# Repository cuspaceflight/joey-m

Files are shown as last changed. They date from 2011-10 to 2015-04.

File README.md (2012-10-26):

JOEY-M - CU Spaceflight
====================

Joey-M is an experimental flight computer produced as part of the Wombat flight
computer project at Cambridge University Spaceflight.  

It uses a twin varactor crystal pulling arrangement to change the transmit
frequency of a Micrel MICRF112YMM 434MHz ISM band transmitter, along with a dual
DAC from Linear Technology to control the varactor bias voltages.  

The DAC can be any of the LTC range in MSOP-8 package which share a footprint, 
including the LTC1661/1662 (10 bit), LTC2622 (12 bit), LTC2612 (14 bit)
and LTC2602 (16 bit).  

Other equipment on board is a uBlox NEO-6Q GPS, TMP100 12 bit temperature
sensor, and an Atmel ATMEGA328P MCU.  

Designed and released into the public domain by Jon Sowman - March 2012.  

[Contact CUSF](mailto:contact@cusf.co.uk)

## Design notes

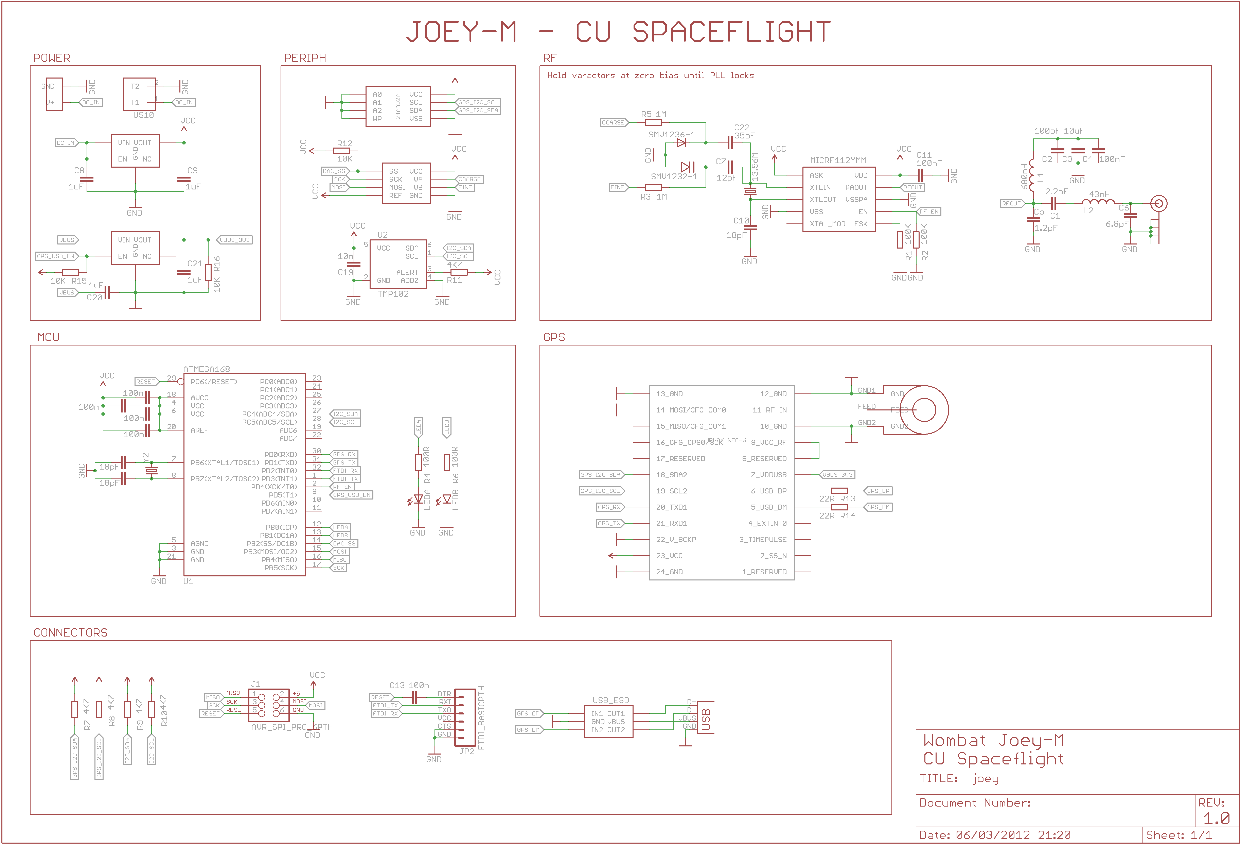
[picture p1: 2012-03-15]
pcb/joey-m.png

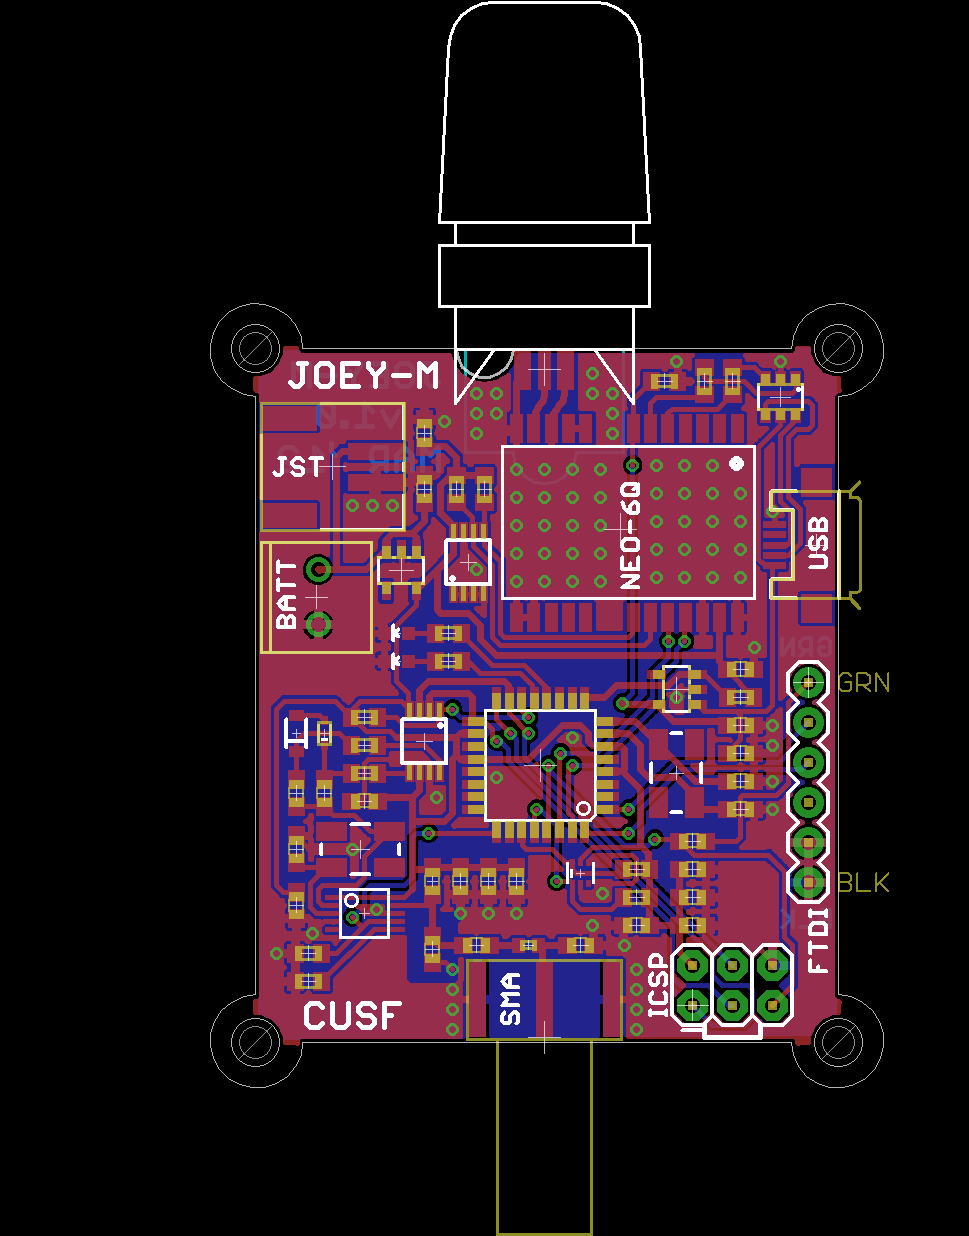
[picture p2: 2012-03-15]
pcb/joey-m-brd.png

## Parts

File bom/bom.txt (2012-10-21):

  PART         QTY             DESCRIPTION               TYPE            LIST
  ==========================================================================
1715486         1       ATMEL AVR ATMEGA328             TQFP32          £4.25
1494165 	1 	MICREL MICRF112YMM UHF    	MSOP10    	£3.28
1753780         1 	RF VARACTOR DIODE SMV1232  	SC79     	£0.74
1753783         1 	RF VARACTOR DIODE SMV1236  	SOD-323     	£0.54
1858064         2       IC, LDO, 3.3V, 0.3A, 5TSOT      5-TSOT          £0.89
1269406         1       ESD PROTECTION, SMD             SOT-23-6        £0.56
1331296         1       24AA32A I2C EEPROM              MSOP8           £0.40
1342651         1       JACK SMA, END LAUNCH            BULKHEAD        £2.93
1234659         1       TMP100 IC, SOT-23-6             SOT23-6         £2.22
1330944         1       DAC, DUAL 16-BIT                MSOP8           £8.88
1098611         1       TERMINAL BLOCK, 2WAY            PTH             £0.21
9492615         1       JST, SIDE ENT, 2WAY             SMD             £0.34
1521869         1       MICRO USB AB RECEPT             SMD             £0.67
1248132         1       ICSP HEADER 2x3 PTH 0.1"        PTH             £0.24
1841236         1       HEADER, 2.54MM, PIN, 32WAY      PTH             £1.88
1841971 	1 	13.56MHz XTAL 5x3mm      	SMD       	£0.59
1640930         1       16.00MHz XTAL 5.3mm             SMD             £1.62
1650686         1       BATT HOLDER AAA, LEADED         N/A             £1.20
-- PASSIVES
1469748         3       RESISTOR 10KR 0.1W              0603            £0.01
1738931         2 	RESISTOR 0.1W 100KR       	0603      	£0.02
9330364         2       RESISTOR 100R                   0603            £
2008367         2       RESISTOR 1MR                    0603            £0.01
2008358         4       RESISTOR 4K7                    0603            £0.01
2008345         2       RESISTOR 22R                    0603            £0.01
1833863         8 	CAPACITOR 100nF           	0603      	£0.01
1833804         1       CAPACITOR, 6.3V, 10UF           0603            £0.15
1833809         4       CAPACITOR 1UF                   0603            £0.02
1327675         1       CAPACITOR 10NF                  0603            £0.02
1748739         1 	INDUCTOR 43nH             	0402      	£0.28
1343111 	1 	INDUCTOR 680nH            	0603      	£0.16
1328308         1       LED RED                         0603            £
1328306         1       LED GREEN                       0603            £
-- C0G CAPS
1865478         1       CAPACITOR 36PF                  0603            £0.01
1828907         1       CAPACITOR 12PF                  0603            £0.01
1414620         3       CAPACITOR 18PF                  0603            £0.03
1865503         1       CAPACITOR 6.8PF                 0603            £0.04
1457729         1       CAPACITOR 1.2PF                 0603            £0.13
1813415         1       CAPACITOR 2.2PF                 0603            £0.03
9406115         1       CAPACITOR 100PF                 0603            £0.02
-- OTHER
SARANTEL SL1202 ANTENNA
UBLOX NEO-6Q GPS

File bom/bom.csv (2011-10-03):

Line Number | Order Code | Qty | Product Description | Manufacturer Name & Part No. | RoHS | List Price | Availability | Line Price | Line note
1 | 1753785 | 2 | RF TUNING VARACTOR DIODE | SKYWORKS SOLUTIONS INC - SMV1249-079LF | YES | 0.4536 | In Stock | 0.91 | RF TUNING VARACTOR DIODE
2 | 1189327 | 1 | CAPACITOR, VARIABLE, 5 TO 20PF | AVX - CTZ2E-20C-W2-P | YES | 0.6237 | In Stock | 0.62 | VARIABLE CAPACITOR 5-20pF
3 | 1865473 | 10 | CAPACITOR, NP0, 0603, 50V, 13PF | KEMET - C0603C130J5GACTU | YES | 0.0105 | In Stock | 0.11 | CAPACITOR 13pF 50V
4 | 1841971 | 1 | XTAL, 13.560MHZ, 18PF, SMD, 5.0X3.2 | TXC - 7B-13.560MAAJ-T | YES | 0.5913 | In Stock | 0.59 | 13.560MHz XTAL 5x3mm
5 | 1494165 | 1 | TRANSMITTER, ASK/FSK, UHF, MSOP10 | MICREL SEMICONDUCTOR - MICRF112YMM | YES | 2.66 | In Stock | 2.66 | MICREL MICRF112YMM UHF
6 | 721852 | 10 | CAPACITOR, 0603, 1.20PF, 50V | YAGEO (PHYCOMP) - CC0603CRNPO9BN1R2 | YES | 0.0275 | In Stock | 0.28 | CAPACITOR 1.2pF
7 | 1343111 | 5 | INDUCTOR, 0603 CASE, SHIELD, 680NH±10% | MURATA - LQM18NNR68K00D | YES | 0.1571 | In Stock | 0.79 | INDUCTOR 680nH
8 | 1650758 | 1 | CAPACITOR, CERAMIC MULTILAYER | JOHANSON TECHNOLOGY - 251R14S2R2BV4T... | YES | 0.0486 | In Stock | 0.05 | CAPACITOR 2.2pF
9 | 8819807 | 10 | CAPACITOR, 0603, 6.8PF, 50V | MURATA - GRM1885C1H6R8DZ01D | YES | 0.0397 | In Stock | 0.4 | CAPACITOR 6.8pF
10 | 9406115 | 10 | CAPACITOR, 0603, 100PF, 50V | MULTICOMP - U0603C101JCT | YES | 0.0154 | In Stock | 0.15 | CAPACITOR 100pF
11 | 1833863 | 10 | CAPACITOR, 0603, X7R, 16V, 100NF | AVX - 0603YC104K4T4A | YES | 0.0122 | In Stock | 0.12 | CAPACITOR 100nF
12 | 1627775 | 10 | RESISTOR, SURGE, 10K, 1%, 0603 | KOA - SG73S1JTTD1002F | Y-EX | 0.0251 | In Stock | 0.25 | RESISTOR 63mW 10KR
13 | 1294515 | 5 | CAPACITOR, 0603, 9.1PF, 200V, C0G | MURATA - ERB1885C2D9R1CDX5D | YES | 0.0494 | In Stock | 0.25 | CAPACITOR 9.1pF
14 | 1738931 | 25 | RESISTOR, 0603, 1%, 100K | VISHAY DRALORIC - CRCW0603100KFKEAHP | Y-EX | 0.0243 | In Stock | 0.61 | RESISTOR 0.1W 100KR
15 | 1668492 | 1 | HEADER, 2.54MM, SINGLE, 4WAY | SAMTEC - TLW-104-05-G-S | YES | 0.4698 | In Stock | 0.47 | 4x1 HEADER PC BOARD
16 | 1748739 | 3 | INDUCTOR, 0402, 43NH, 100MA | WUERTH ELEKTRONIK - 744765143A | YES | 0.2754 | In Stock | 0.83 | INDUCTOR 43nH
17 | 1463375 | 2 | CAPACITOR, 0603, 10UF, 6.3V, X5R | TAIYO YUDEN - JMK107BJ106MA-T | YES | 0.4455 | In Stock | 0.89 | CAPACITOR 10uF
 |  |  |  |  |  |  | Goods Subtotal: | 9.98
 |  |  |  |  |  |  | Promotion Code Discount: | 0.0
 |  |  |  |  |  |  | Delivery Charges | Unknown
 |  |  |  |  |  |  | Your Total Price: | 9.98
 |  |  |  |  |  |  | VAT | 2.0
 |  |  |  |  |  |  | Total (Excl Delivery) | 11.98

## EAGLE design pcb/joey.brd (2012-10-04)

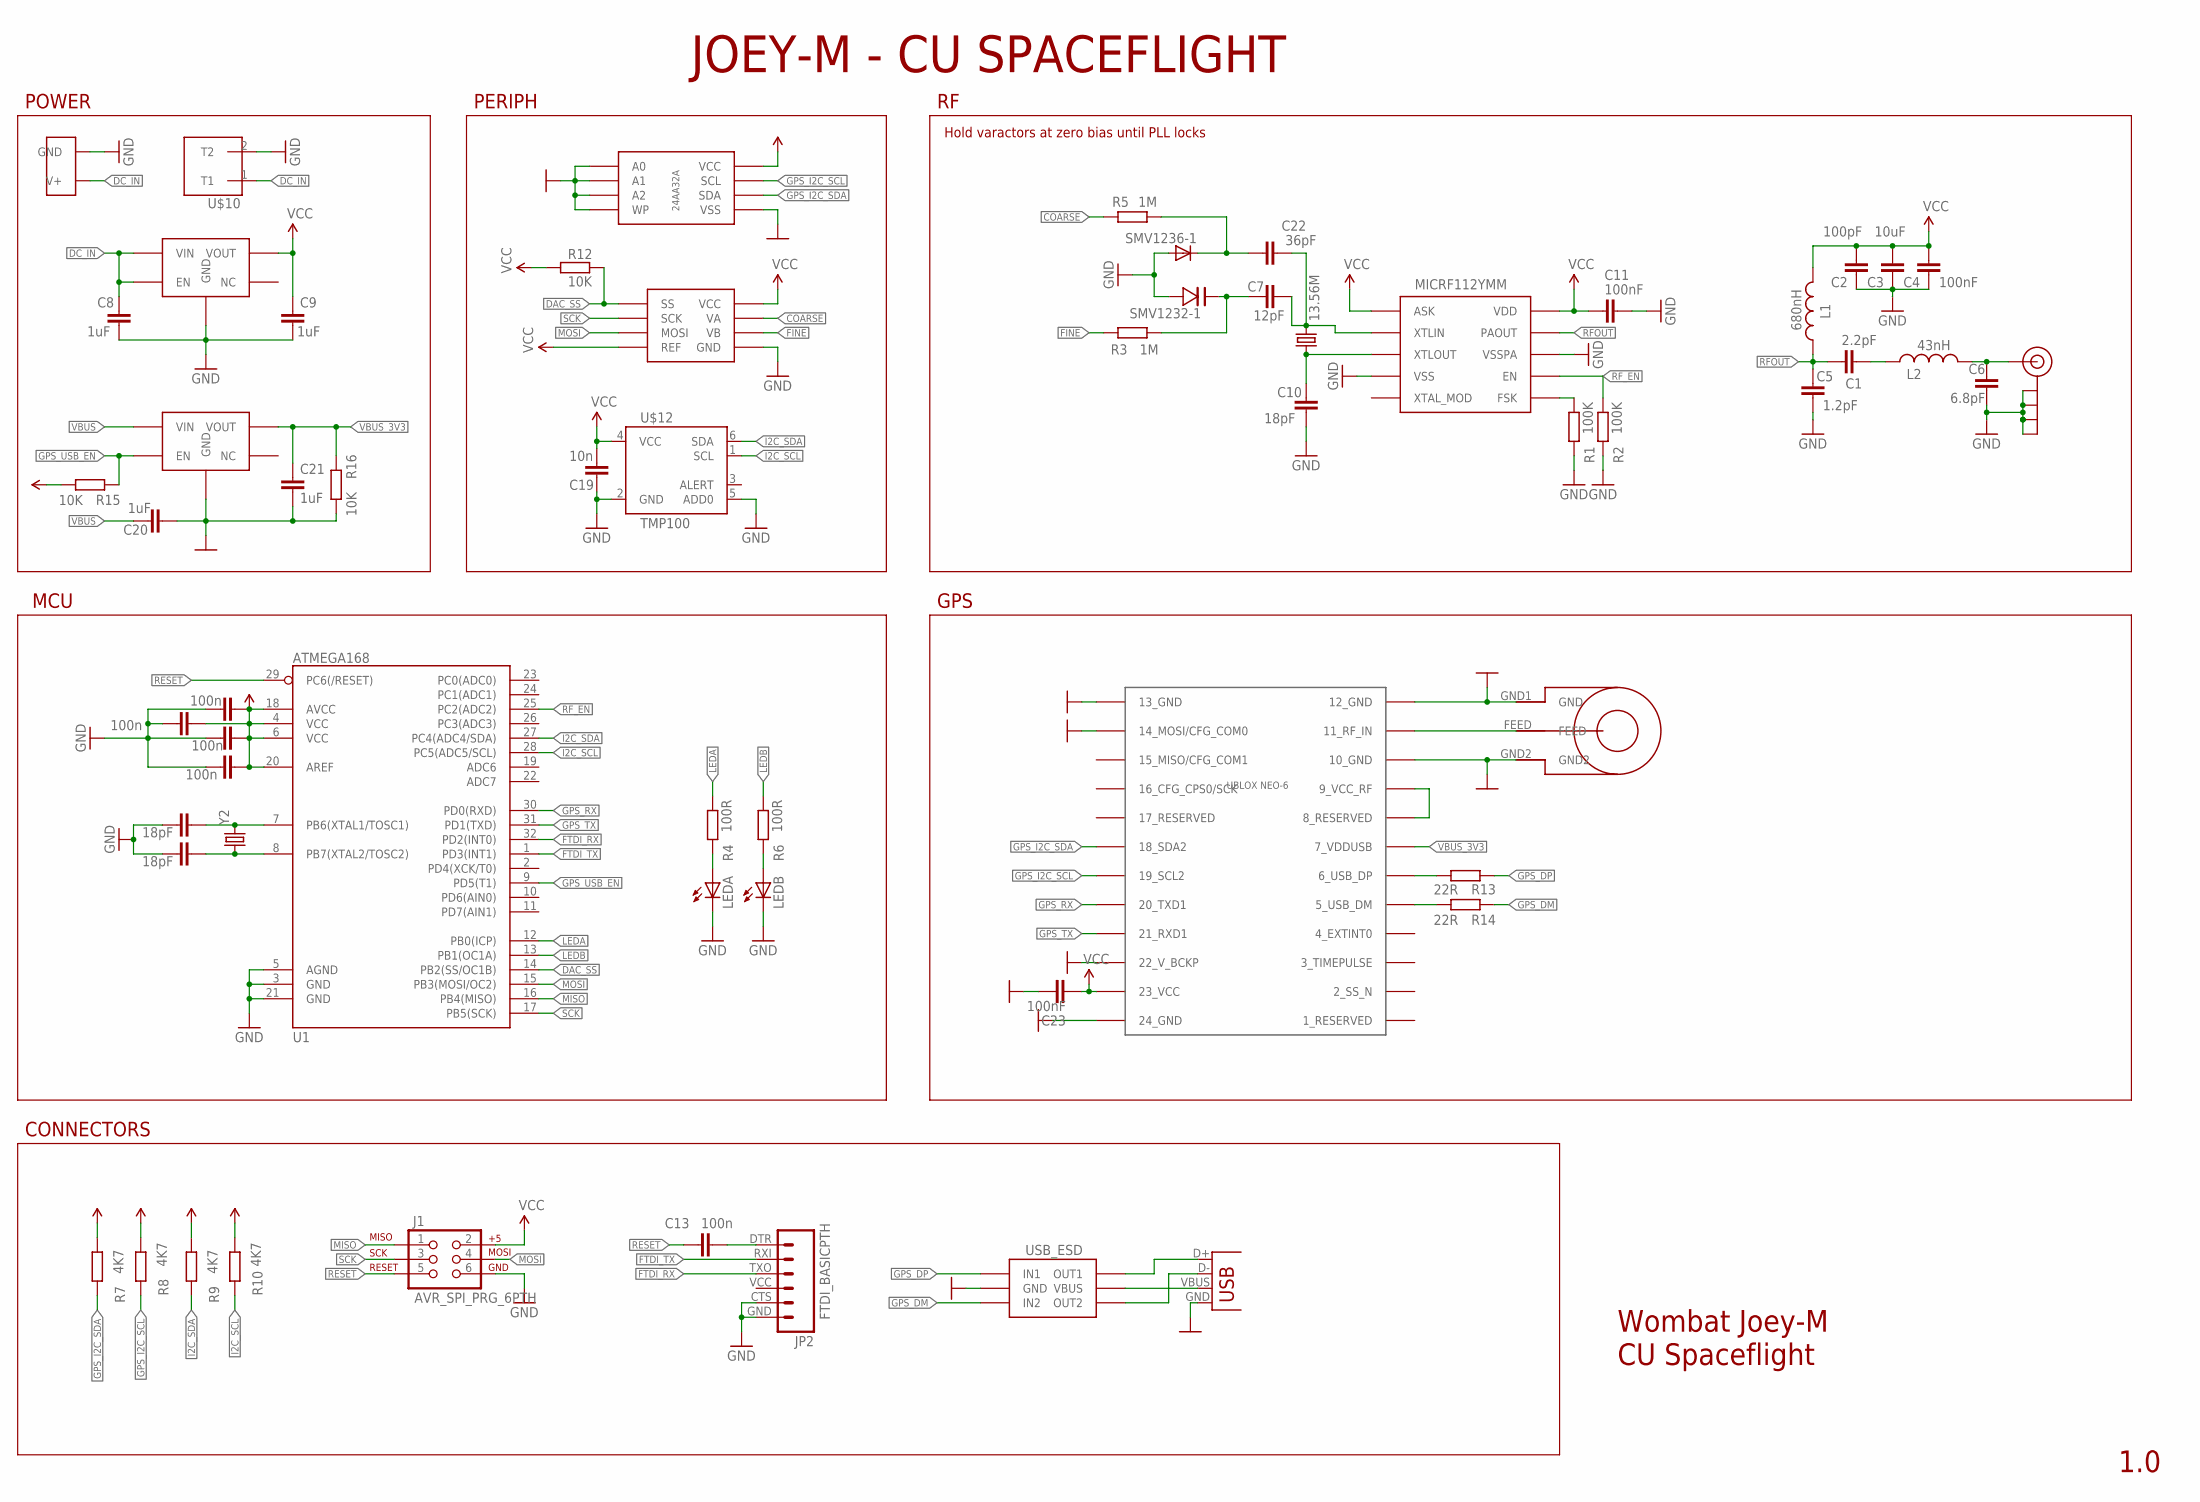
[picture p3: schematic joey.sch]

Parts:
C1: 2.2pF; C0603
C2: 100pF; C0603
C3: 10uF; C0603
C4, C11, C23: 100nF; C0603
C5: 1.2pF; C0603
C6: 6.8pF; C0603
C7: 12pF; C0603
C8, C9, C20, C21: 1uF; C0603
C10, C17, C18: 18pF; C0603
C12, C13, C14, C15, C16: 100n; C0603
C19: 10n; C0603
C22: 36pF; C0603
J1: AVR_SPI_PRG_6PTH; 2X3
JP2: FTDI_BASICPTH; FTDI_BASIC
L1: 680nH; 0603
L2: 43nH; C0402
LEDA: LED0603; LED-0603
LEDB: LED0603; LED-0603
R1, R2: 100K; R0603
R3, R5: 1M; R0603
R4, R6: 100R; R0603
R7, R8, R9, R10: 4K7; R0603
R12, R15, R16: 10K; R0603
R13, R14: 22R; R0603
SMV1232-1: SMV1247-VARACTOR; SMV1247-VARACTOR-SC-79
SMV1236-1: DIODESOD; SOD-323
U1: ATMEGA168; TQFP32-08
U$1: MICRF112; MICRF112-MSOP10
U$2: SARANTEL-SR1202
U$3: UBLOX_NEO-6; UBLOX_NEO-6P
U$4, U$9: ADP122AUJZ-3V3REG-5TSOT; SOT23-5L
U$5: JST_SMTSIDE; JST_CONN_SMD
U$6: I2C_EEPROM_24AA32A; MSOP8
U$7: SMA_END_19-70-TGG
U$8: LTC2602_16BIT_DUALDAC; MSOP8
U$10: TE_CONN_TERMBLK; 10A_TECONN_TERMBLK
U$12: TMP100; SOT23-6
USB_ESD: USB_ESD_PROT_USBLC6; SOT23-6
X1: USB-MICROB
Y1: 13.56M; CRYSTAL-SMD-5X3
Y2: CRYSTAL5X3; CRYSTAL-SMD-5X3

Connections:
COARSE: R5.1, U$8.8 (VA)
COARSE_V: C22.1, R5.2, SMV1236-1.1 (C)
DAC_SS: R12.2, U1.14 (PB2(SS/OC1B)), U$8.1 (SS)
DC_IN: C8.2, U$4.1 (VIN), U$4.3 (EN), U$5.VBATT (V+), U$10.1 (T1)
FINE: R3.2, U$8.5 (VB)
FTDI_RX: JP2.TXO (3), U1.32 (PD2(INT0))
FTDI_TX: JP2.RXI (2), U1.1 (PD3(INT1))
GND: C2.1, C3.1, C4.1, C5.1, C6.1, C8.1, C9.1, C10.1, C11.1, C12.2, C14.1, C15.1, C16.1, C17.2, C18.2, C19.1, C20.1, C21.1, C23.1, J1.6, JP2.CTS (5), JP2.GND (6), LEDA.C, LEDB.C, R1.1, R2.1, R16.2, SMV1232-1.AN (ANODE), SMV1236-1.2 (A), U1.3 (GND), U1.5 (AGND), U1.21 (GND), U$1.VSS, U$1.VSSPA, U$2.GND1 (GND), U$2.GND2, U$3.10_GND, U$3.12_GND, U$3.13_GND, U$3.14_MOSI/CFG_COM0, U$3.22_V_BCKP, U$3.24_GND, U$4.2 (GND), U$5.GND, U$6.1 (A0), U$6.2 (A1), U$6.3 (A2), U$6.4 (VSS), U$6.7 (WP), U$7.GND1 (GND), U$7.GND2 (GND), U$7.GND3 (GND), U$7.GND4 (GND), U$8.7 (GND), U$9.2 (GND), U$10.2 (T2), U$12.2 (GND), U$12.5 (ADD0), USB_ESD.2 (GND), X1.GND
GPS_DM: R14.1, USB_ESD.3 (IN2)
GPS_DP: R13.1, USB_ESD.1 (IN1)
GPS_I2C_SCL: R8.1, U$3.19_SCL2, U$6.6 (SCL)
GPS_I2C_SDA: R7.1, U$3.18_SDA2, U$6.5 (SDA)
GPS_RX: U1.30 (PD0(RXD)), U$3.20_TXD1
GPS_TX: U1.31 (PD1(TXD)), U$3.21_RXD1
GPS_USB_EN: R15.1, U1.9 (PD5(T1)), U$9.3 (EN)
I2C_SCL: R10.1, U1.28 (PC5(ADC5/SCL)), U$12.1 (SCL)
I2C_SDA: R9.1, U1.27 (PC4(ADC4/SDA)), U$12.6 (SDA)
LEDA: R4.2, U1.12 (PB0(ICP))
LEDB: R6.2, U1.13 (PB1(OC1A))
MISO: J1.1, U1.16 (PB4(MISO))
MOSI: J1.4, U1.15 (PB3(MOSI/OC2)), U$8.3 (MOSI)
unnamed: R1.2, U$1.FSK
unnamed: C10.2, U$1.XTLOUT, Y1.1
unnamed: C13.2, JP2.DTR (1)
unnamed: C7.2, C22.2, U$1.XTLIN, Y1.3 (2)
unnamed: C1.2, L2.1
unnamed: C6.2, L2.2, U$7.RF (SIGNAL)
unnamed: C7.1, R3.1, SMV1232-1.CAT (CATHODE)
unnamed: LEDA.A, R4.1
unnamed: C17.1, U1.7 (PB6(XTAL1/TOSC1)), Y2.3 (2)
unnamed: C18.1, U1.8 (PB7(XTAL2/TOSC2)), Y2.1
unnamed: U$2.FEED, U$3.11_RF_IN
unnamed: LEDB.A, R6.1
unnamed: U$3.8_RESERVED, U$3.9_VCC_RF
unnamed: USB_ESD.4 (OUT2), X1.D-
unnamed: USB_ESD.6 (OUT1), X1.D+
unnamed: R13.2, U$3.6_USB_DP
unnamed: R14.2, U$3.5_USB_DM
RESET: C13.1, J1.5, U1.29 (PC6(/RESET))
RFOUT: C1.1, C5.2, L1.1, U$1.PAOUT
RF_EN: R2.2, U1.25 (PC2(ADC2)), U$1.EN
SCK: J1.3, U1.17 (PB5(SCK)), U$8.2 (SCK)
VBUS: C20.2, U$9.1 (VIN), USB_ESD.5 (VBUS), X1.VBUS
VBUS_3V3: C21.2, R16.1, U$3.7_VDDUSB, U$9.5 (VOUT)
VCC: C2.2, C3.2, C4.2, C9.2, C11.2, C12.1, C14.2, C15.2, C16.2, C19.2, C23.2, J1.2, L1.2, R7.2, R8.2, R9.2, R10.2, R12.1, R15.2, U1.4 (VCC), U1.6 (VCC), U1.18 (AVCC), U1.20 (AREF), U$1.ASK, U$1.VDD, U$3.23_VCC, U$4.5 (VOUT), U$6.8 (VCC), U$8.4 (REF), U$8.6 (VCC), U$12.4 (VCC)

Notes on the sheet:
Wombat Joey-M
CU Spaceflight
1.0
Hold varactors at zero bias until PLL locks
JOEY-M - CU SPACEFLIGHT
POWER
MCU
GPS
PERIPH
CONNECTORS

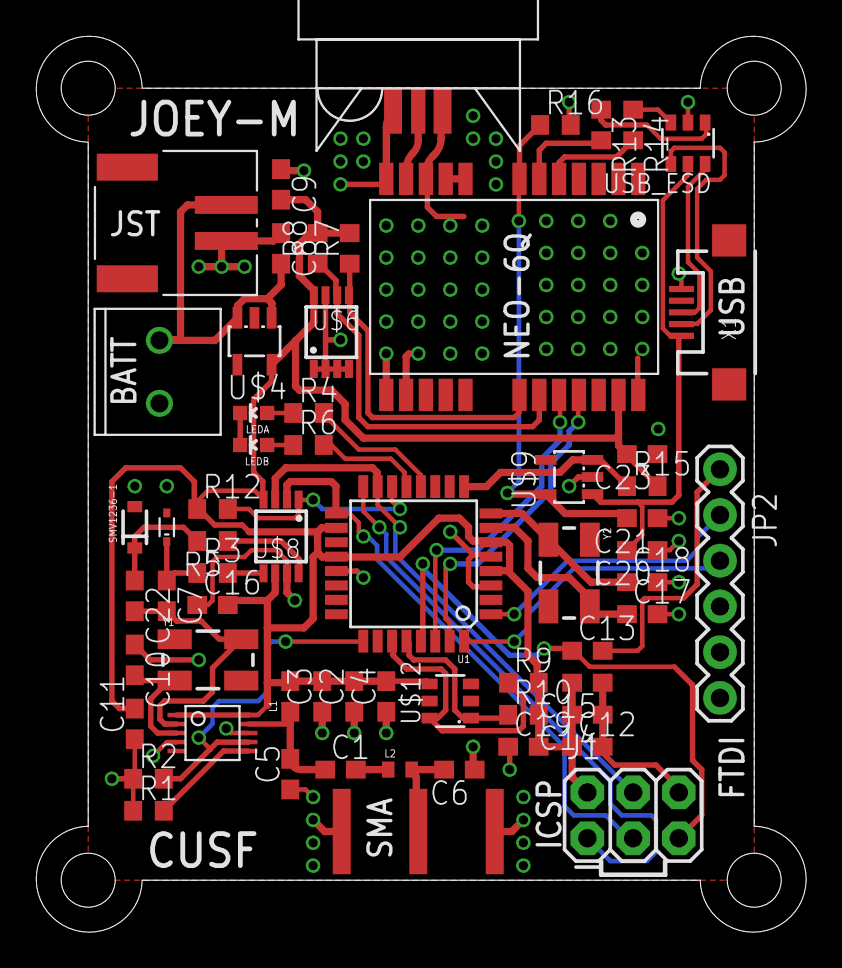
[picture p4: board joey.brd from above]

Board: 2 copper layers, 42.8 x 49.8 mm, 63 parts (1 on the bottom side), 45 nets.

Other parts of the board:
U$11: CUSF_LOGO_LARGE

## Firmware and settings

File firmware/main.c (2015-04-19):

/**
 * JOEY-M by CU Spaceflight
 *
 * This file is part of the JOEY-M project by Cambridge University Spaceflight.
 *
 * Jon Sowman 2012
 */

#include <avr/io.h>
#include <stdio.h>
#include <util/delay.h>
#include <avr/eeprom.h>
#include <avr/interrupt.h>
#include <string.h>
#include <stdbool.h>
#include <stdlib.h>
#include <avr/wdt.h>

#include "led.h"
#include "radio.h"
#include "gps.h"

// 30kHz range on COARSE, 3kHz on FINE

char s[100];
uint32_t EEMEM ticks = 0;

int main()
{
    // Disable, configure, and start the watchdog timer
    wdt_disable();
    wdt_reset();
    wdt_enable(WDTO_8S);

    // Start and configure all hardware peripherals
    sei();
    led_init();
    radio_init();
    gps_init();
    radio_enable();

    // Set the radio shift and baud rate
    _radio_dac_write(RADIO_COARSE, RADIO_CENTER_FREQ);
    _radio_dac_write(RADIO_FINE, 0);
    radio_set_shift(RADIO_SHIFT_425);
    radio_set_baud(RADIO_BAUD_50);

    // Radio chatter
    for(uint8_t i = 0; i < 5; i++)
    {
        radio_chatter();
        wdt_reset();
    }
    
    int32_t lat = 0, lon = 0, alt = 0;
    uint8_t hour = 0, minute = 0, second = 0, lock = 0, sats = 0;

    while(true)
    {
        led_set(LED_GREEN, 1);

        // Get the current system tick and increment
        uint32_t tick = eeprom_read_dword(&ticks) + 1;

        // Check that we're in airborne <1g mode
        if( gps_check_nav() != 0x06 ) led_set(LED_RED, 1);

        // Get information from the GPS
        gps_check_lock(&lock, &sats);
        if( lock == 0x02 || lock == 0x03 || lock == 0x04 )
        {
            gps_get_position(&lat, &lon, &alt);
            gps_get_time(&hour, &minute, &second);
        }

        led_set(LED_GREEN, 0);

        // Format the telemetry string & transmit
        double lat_fmt = (double)lat / 10000000.0;
        double lon_fmt = (double)lon / 10000000.0;
        alt /= 1000;

        sprintf(s, "$$" CALLSIGN ",%lu,%02u:%02u:%02u,%02.7f,%03.7f,%ld,%u,%x",
            tick, hour, minute, second, lat_fmt, lon_fmt, alt,
            sats, lock);
        radio_chatter();
        radio_transmit_sentence(s);
        radio_chatter();

        led_set(LED_RED, 0);
        eeprom_update_dword(&ticks, tick);
        wdt_reset();
        _delay_ms(500);
    }

    return 0;
}

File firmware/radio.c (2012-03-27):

/**
 * JOEY-M by CU Spaceflight
 *
 * This file is part of the JOEY-M project by Cambridge University Spaceflight.
 *
 * Jon Sowman 2012
 */

#include <stdio.h>
#include <string.h>
#include <avr/io.h>
#include <util/delay.h>
#include <avr/interrupt.h>
#include <avr/eeprom.h>
#include <avr/wdt.h>
#include <util/crc16.h>
#include "stdbool.h"
#include "led.h"
#include "radio.h"

uint16_t _radio_shift = 0x0000;

volatile uint16_t _dac_value = 0;
volatile uint8_t sample = 0;
volatile int32_t _transition_delta = 0;
volatile uint16_t _transition_start = 0;
volatile bool transition_complete = true;

// RTTY stuff
volatile uint8_t systicks = 0;
volatile uint8_t _txbyte = 0;
volatile uint8_t _txptr = 0;
volatile bool byte_complete = false;

uint8_t EEMEM step[50] = {4, 7, 11, 15, 19, 23, 28, 32, 37, 42, 47, 52, 57, 
    62, 67, 73, 78, 84, 90, 95, 101, 107, 113, 119, 125, 130, 136, 142, 148,
    154, 160, 165, 171, 177, 182, 188, 193, 198, 203, 208, 213, 218, 223, 227, 
    232, 236, 240, 244, 248, 251};

/**
 * Initialise the radio subsystem including the dual 16 bit 
 * DAC.
 */
void radio_init(void)
{
    // Configure the slave select pin and set it high
    RADIO_DDR |= _BV(RADIO_SS) | _BV(RADIO_MOSI) | _BV(RADIO_SCK);
    RADIO_DDR &= ~(_BV(RADIO_MISO));
    RADIO_PORT |= _BV(RADIO_SS);

    // Set MSB first, sample on rising edge, 
    // clock idles low
    SPCR &= ~(_BV(DORD) | _BV(CPOL) | _BV(CPHA));

    // Enable SPI, set master mode and fosc/2, giving an SPI
    // interface SCK speed of 8MHz
    SPSR |= _BV(SPI2X);
    SPCR &= ~(_BV(SPR0) | _BV(SPR1));
    SPCR |= _BV(MSTR) | _BV(SPE);

    // Set up TIMER0 to tick once per symbol and interrupt
    // CTC mode
    TCCR0A |= _BV(WGM01);

    // Prescale by 1024
    TCCR0B |= _BV(CS02) | _BV(CS00);

    // Interrupt on compare match with OCR0A
    OCR0A = 156;

    // Set up TIMER2 for the DSP (!) stuff
    // No clock prescale to get 62.5kHz sample rate with an 8 bit timer
    TCCR2B |= _BV(CS20);

    // Do not interrupt on overflow for now
    TIMSK2 &= ~(_BV(TOIE2));

    // Turn off the DAC
    _radio_dac_off();

    // Enable global interrupts
    sei();
}

/**
 * Enable the power amplifier on the Micrel radio
 */
void radio_enable(void)
{
    RADIO_EN_DDR |= _BV(RADIO_EN);
    RADIO_EN_PORT |= _BV(RADIO_EN);
    _delay_ms(100);
}

/**
 * Disable the power amp on the Micrel radio to shut it down
 */
void radio_disable(void)
{
    RADIO_EN_DDR |= _BV(RADIO_EN);
    RADIO_EN_PORT &= ~(_BV(RADIO_EN));
}

/**
 * Write a value to one of the DAC channels
 */
void _radio_dac_write(uint8_t channel, uint16_t value)
{
    // Take SS low
    RADIO_PORT &= ~(_BV(RADIO_SS));

    // Write cmd then value to the SPI data register
    SPDR = 0x30 | (channel & 0x01);
    while(!(SPSR & _BV(SPIF)));
    SPDR = value >> 8;
    while(!(SPSR & _BV(SPIF)));
    SPDR = value & 0xFF;
    while(!(SPSR & _BV(SPIF)));

    // Raise SS to signal end of transaction
    RADIO_PORT |= _BV(RADIO_SS);

    // Update the DAC value
    if(channel == RADIO_FINE) _dac_value = value;
}

/**
 * Power down the DAC and set the outputs to a high-Z state
 */
void _radio_dac_off(void)
{
    // Take SS low
    RADIO_PORT &= ~(_BV(RADIO_SS));

    // Write cmd then value to the SPI data register
    SPDR = 0x4F;
    while(!(SPSR & _BV(SPIF)));
    SPDR = 0;
    while(!(SPSR & _BV(SPIF)));
    SPDR = 0;
    while(!(SPSR & _BV(SPIF)));

    // Raise SS to signal end of transaction
    RADIO_PORT |= _BV(RADIO_SS);
}

/**
 * Transmit the given string over the radio terminated with a checksum
 * and a newline, compatible with the UKHAS habitat listener and parser.
 */
void radio_transmit_sentence(char* string)
{
    radio_transmit_string(string);
    
    // Calculate the checksum and send it
    uint16_t checksum = radio_calculate_checksum(string);
    char cs[7];
    sprintf(cs, "*%04X\n", checksum);
    radio_transmit_string(cs);
}


/**
 * Transmit a null terminated string over the radio link.
 */
void radio_transmit_string(char* string)
{
    while(*string)
    {
        _txbyte = *string;
        _txptr = 0;
        byte_complete = false;
        TIMSK0 |= _BV(OCIE0A);
        while(!byte_complete);
        wdt_reset();
        string++;
    }
}

/**
 * Set the radio shift
 */
void radio_set_shift(uint16_t shift)
{
    _radio_shift = shift;
}

/**
 * Set the baud rate by setting the compare value for TIMER0
 */
void radio_set_baud(uint8_t baud)
{
    OCR0A = baud;
}

/**
 * Transition using the FIR filter
 */
void _radio_transition(uint16_t target)
{
    if( _dac_value == target ) return;

    // Update the global target and initial
    _transition_start = _dac_value;
    _transition_delta = (int32_t)target - (int32_t)_transition_start;
    transition_complete = false;

    // Start the DSP timer interrupting
    TIMSK2 |= _BV(TOIE2);
}

/**
 * Transmit a single bit at a pointer, also coping with start and 
 * stop bits.
 */
void _radio_transmit_bit(uint8_t data, uint8_t ptr)
{
    if(ptr == 0)
        _radio_transition(0);
    else if(ptr >= 1 && ptr <= 8)
        if( (data >> (ptr - 1)) & 1 )
            _radio_transition(_radio_shift);
        else
            _radio_transition(0);
    else
        _radio_transition(_radio_shift);
}

/**
 * Calculate the checksum for the radio string excluding any $ signs
 * at the start.
 */
uint16_t radio_calculate_checksum(char* data)
{
    uint16_t i;
    uint16_t crc = 0xFFFF;

    for (i = 0; i < strlen(data); i++) {
        if (data[i] != '$') crc = _crc_xmodem_update(crc,(uint8_t)data[i]);
    }
    return crc;
}

/**
 * Make some noise on the radio on the 2FSK tones as a pre/post amble
 * such that Joey can be easily identified.
 */
void radio_chatter(void)
{
    _radio_dac_write(RADIO_FINE, 0x0000);
    _delay_ms(200);
    _radio_dac_write(RADIO_FINE, _radio_shift);
    _delay_ms(200);
    _radio_dac_write(RADIO_FINE, 0x0000);
    _delay_ms(200);
    _radio_dac_write(RADIO_FINE, _radio_shift);
    _delay_ms(200);
}

/**
 * Interrupt handle for the radio timer, when we reach the systicks
 * limit we should transmit the next bit
 */
ISR(TIMER0_COMPA_vect)
{
    if( systicks < 1 )
    {
        systicks++;
    }
    else
    {
        if( _txptr < 11 )
        {
            _radio_transmit_bit(_txbyte, _txptr);
            _txptr++;
        } else {
            TIMSK0 &= ~(_BV(OCIE0A));
            byte_complete = true;
        }
        systicks = 0;
    }
}

/**
 * Interrupt handler for the DSP timer. Read out the next step
 * response value and write it to the DAC.
 */
ISR(TIMER2_OVF_vect)
{
    if( sample < DSP_SAMPLES )
    {
        int32_t d = _transition_delta * (int32_t)(eeprom_read_byte(&step[sample]));
        d /= 256;
        d += (int32_t)_transition_start;
        _radio_dac_write(RADIO_FINE, (uint16_t)d);
        sample++;
    } else {
        TIMSK2 &= ~(_BV(TOIE2));
        sample = 0;
        transition_complete = true;
    }
}

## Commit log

2011-10-07 Added values to caps and added the varactor datasheet
    [breakout.brd, breakout.sch]
2012-03-07 First commit of joey-m
    [breakout.brd, breakout.sch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]
2012-03-07 Added remaining board files
    [joey.brd, joey.sch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]
2012-03-08 Fixed filter bug in the schematic, almost finished routing
    [joey.brd, joey.sch]
2012-03-08 Finished routing for v1.0
    [joey.brd]
2012-03-10 Finished routing, updated completed BOM for v1.0
    [joey.brd, joey.sch]
2012-03-10 Fixed green LED part no
2012-03-11 Added some final silk and generated gerbers for 1.0
    [joey.brd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]
2012-03-15 PNGs of schematic and board
2012-03-18 Fixed the varactor grounding bug in v1.0
    [joey.brd, joey.sch]
2012-03-18 Started work on interrupt driven radio code
2012-03-19 upped the DAC SPI interface speed to 8M
2012-03-20 Interrupt driven RTTY decoding proeprly
2012-03-20 Switch to a Gaussian filter window
2012-03-22 Working POSLLH parsing code from GPS, added filter eep binary
2012-03-22 Added gps_num_sats() to get the current number of sats the GPS is tracking
2012-03-23 Fixed things for a 2 byte length field, working lat, long, alt, time, no of sats and lock quality
    [main.c]
2012-03-23 Started work on TMP102 code but it's not working yet
    [main.c]
2012-03-23 Actually added the temperature stuff...
2012-03-26 Fixed number of sats and tidied up the GPS code a bit. still working on temp sensor
    [main.c]
2012-03-26 Enabled the watchdog timer
2012-03-26 Moved global defs to invididual files, dunno why I didn't do that from the start really
    [led.h, main.c, radio.c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]
2012-03-26 Added watchdog timer resetting after each byte transmitted over radio as otherwise 50 baud causes it to to time out, aah
    [main.c, radio.c, radio.h]
2012-03-26 Checked for correct nav mode - airborne <1g, but doesn't actually do anything if it's wrong
    [main.c]
2012-03-27 Added some radio chatter to make Joey easier to find when powering up and to identify by ear during telemetry transmissions
2012-03-29 Added telem log and raw sentence parser from nova 21
    [telemetry.csv]
2012-03-29 Moved gerbers to pcb/
2012-04-02 python script to make a KML file, required simplekml
    [telemetry.csv]
2012-08-08 New crystal, updated some defines to match and correct the shift
    [main.c, radio.h]
2012-10-04 Started doing r2
    [joey.brd]
2012-10-04 Finished rev2 of Joey, submission to CCC at this SHA1
    [joey.brd, joey.sch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]
2012-10-10 Added batt holder to bom
2012-10-21 Switched the 10UF cap for one that farnell still stocks
2012-10-26 Removed the temperature stuff since I want to start it from scratch
2012-10-26 Added some comments to the LED files
2012-11-02 Empty files for the temperature stuff
2012-11-09 Continued working on temp sensor stuff. Need to decide to to determine the end of transmission from the slave
2012-11-16 in theory a complete tmp100 interrupt driven implementation. it compiles, therefore it works. right. right?
2012-11-23 Fixed a typo causing the temp interrupt system to break completely
    [main.c]
2012-11-23 Just tidying some bits for testing the temp sensor, disabled all other functionality for now
2012-12-13 Working temp sensor though the values are a tad weird
2014-08-12 re-enable the watchdog timer
2015-04-19 temperature sensor is broken below -19C
    [main.c]
